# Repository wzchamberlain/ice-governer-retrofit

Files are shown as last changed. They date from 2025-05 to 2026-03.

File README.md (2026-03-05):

# ICE-Governor-Retrofit

## Rationale & Goal

The goal of this project is to provide a low cost electronic governor retrofit for small/carburetor engines to replace poor, worn, malfunctioning, or destroyed governors. Typical off-the-shelf variants cost in excess of $100 USD, surpassing the remaining value of the small engine they might be applied to. The target deployment engine this project is built for specifically is a 4000W single phase (true) generator, where the engine must be kept at a steady 3600 RPM or 3000 RPM for 60 Hz or 50 Hz respectively. Provisions should be made in the design to allow for dynamic target speed setting both for fine tuning or for a dynamic governor, such as in a small tractor or ride on lawnmower, perhaps even a gas powertool.

## Pin Count

### Pin Planning
Max IO: 6 pins. One of the potentiometers should be limited to range of 2.5V to HIGH so that I can be used on the RESET line of the ATTiny (GROUND/LOW Pull is reset active).
1. Spark Detect +
    - Bit 2 (Pin7) is the external interrupt pin and would be preferred, however there is only one external interrupt.
2. Spark Detect -
    - Bit 0 (Pin 5) for convince, has Pin Change Interrupt.
3. Servo PWM
    - Bit 4 or Bit 1 should be used for the non-inverted PWM output.
    - Pin 6 or Pin 3.
4. Speed (Position) Potentiometer
    - Potentiometer for speed
    - (Optional) Grounding/High switch to signal off.
        - Cannot be on reset (Bit 5, Pin 1)
5. Integral Potentiometer
6. Derivative Potentiometer

### Signaled Shutoff Plan
This variant of the schematic and pin planning uses the switch (SPDT) to signal the ATTiny to ramp down (and stall) the engine before entering a sleep state. This will result in a parasitic draw when in sleep/off to allow the microcontroller to wake up and for the LDO Voltage Regulator to down-regulate the battery. This is done as a trade off to make operation safer by ensuring that the throttle body is closed to prevent a runaway. The battery planned is a relatively larger 9V box battery.

#### By Pin Number
1. Second Order Reaction
2. First Order Reaction
3. Speed Set and Sleep Trigger
4. GND
5. Spark Trigger
6. Servo Position PWM
7. Spark Trigger
8. VCC

#### By Port Number (All Port B)
0. Spark Trigger
1. Servo Position PWM
2. Spark Trigger
3. First Order Reaction
4. Speed Set and Sleep Trigger
5. Second Order Reaction

#### Schematic Plan
Schematic

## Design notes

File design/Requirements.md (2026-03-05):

# Requirements Design Document
This document outlines the requirements of this project in order to complete the goal of providing a electronic throttle governance (by speed) retrofit for small engines.
At the writing of this section, previous considerations had been made and hardware selections made. As such this document regards **software requirements** under the constraints of the previously selected hardware rather than the *hardware requirements* that dictated the hardware selections.

## Functional Requirements
These are the functional objectives that the software must achieve.

1. Produce a PWM signal at 50 Hz (t=20 ms) with duty cycle of 1-2 ms (5-10 %) to control throttle positioning servo (sg90).
2. Time spark pulse intervals.
3. Mark spark pulse polarities to eliminate transience.
4. Analog read for speed set point. *Alteratively as Position Error constant.*
5. Interrupt read on speed set to enable sleep-wake behaviour.
6. Analog read for corrective response speed/aggression. *Alternatively as Integral Error constant.*
7. Analog read for corrective response dampening. *Alternatively as Derivative Error constant.*

## Assignments of functions on ATTiny85
The ATTiny85 provides all the needed functional peripherals to achieve these functions, but they must be configured to connect the bus functions and peripheral components as such.

Needed peripheral assignments:

| Function/Peripheral | Count | Reason/Assignment | Port Number(s) | Pin Number(s) |
| ---: | ----: | :--- | ---: | ---: |
| PWM (Timer with prescale and dedicated reset output) | 1x | PWM to pin for throttle servo control signal. Outputs directly to pin. | 1 | 6x |
| Timer (with prescale) | 1x | For measurement of timing of spark pulses (for engine speed calculation and Process). No physical IO, logically controlled by software interrupts. | N/A | N/A |
| PCINT (Process Interrupt) | 2x | For catchment of spark trigger events. Mapped to spark sense pins. | 0, 2 | 5, 7 |
| PCINT/INT | 1x (Assigned on sleep) | For wake from sleep state. Mapped to speed/proportion response pin. | 4 | 3 |
| ADC | 3x | ADC measurement of trim potentiometers for adjustment of Set Point and/or PID constants | 3, 4, 5 | 1, 2, 3 |

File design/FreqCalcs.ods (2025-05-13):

RPM | Hz | T/c (s) | 1/2 RPM | 1/2 Hz | 2 T/c (s) | Delta T/c (s) | Delta 2T/c (s) | Delta T/c (ms) | Delta 2T/c (ms) | Delta T/c (μm) | Delta 2T/c (μm) | Delta T/c (ns) | Delta 2T/c (ns) | c/1MHz | c/4MHz | c/10MHz | c/20MHz | 2c/1MHz | 2c/4MHz | 2c/10MHz | 2c/20MHz
10 | 0.166666666666667 | 6 | 5 | 0.0833333333333333 | 12 | 3 | 6 | 3000 | 6000 | 3000000 | 6000000 | 3000000000 | 6000000000 | 6000000 | 24000000 | 60000000 | 120000000 | 12000000 | 48000000 | 120000000 | 240000000
20 | 0.333333333333333 | 3 | 10 | 0.166666666666667 | 6 | 1 | 2 | 1000 | 2000 | 1000000 | 2000000 | 1000000000 | 2000000000 | 3000000 | 12000000 | 30000000 | 60000000 | 6000000 | 24000000 | 60000000 | 120000000
30 | 0.5 | 2 | 15 | 0.25 | 4 | 0.5 | 1 | 500 | 1000 | 500000 | 1000000 | 500000000 | 1000000000 | 2000000 | 8000000 | 20000000 | 40000000 | 4000000 | 16000000 | 40000000 | 80000000
40 | 0.666666666666667 | 1.5 | 20 | 0.333333333333333 | 3 | 0.3 | 0.6 | 300 | 600 | 300000 | 600000 | 300000000 | 600000000 | 1500000 | 6000000 | 15000000 | 30000000 | 3000000 | 12000000 | 30000000 | 60000000
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

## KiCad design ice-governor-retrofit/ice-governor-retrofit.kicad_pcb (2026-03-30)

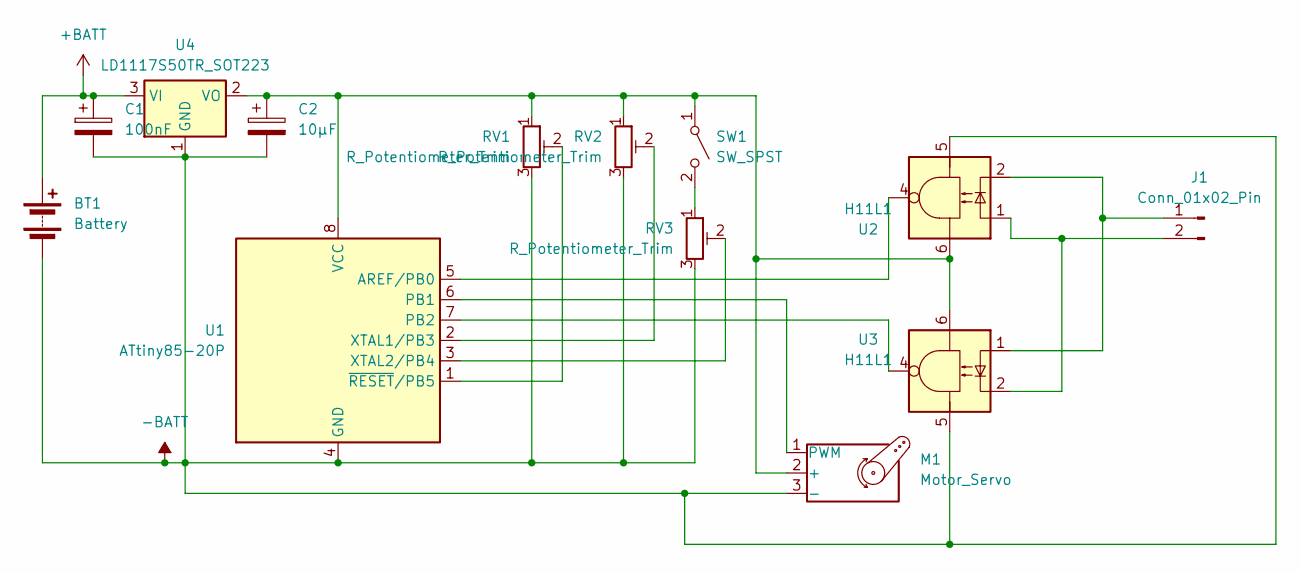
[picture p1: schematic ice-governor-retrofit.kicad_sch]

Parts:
BT1: Battery; BatteryHolder_Eagle_12BH611-GR
C1: 100nF; CP_Radial_D5.0mm_P2.50mm
C2: 10μF; CP_Radial_D5.0mm_P2.50mm
J1: Conn_01x02_Pin; PinHeader_1x02_P2.54mm_Vertical
M1: Motor_Servo; PinHeader_1x03_P2.54mm_Vertical
RV1, RV2, RV3: R_Potentiometer_Trim; Potentiometer_Vishay_43_Horizontal
SW1: SW_SPST; PinHeader_1x02_P2.54mm_Vertical
U1: ATtiny85-20P; DIP-8_W7.62mm
U2, U3: H11L1; DIP-6_W7.62mm
U4: LD1117S50TR_SOT223; SOT-223-3_TabPin2

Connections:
+BATT: BT1.1 (+), C1.1, U4.3 (VI)
-BATT: BT1.2 (-), C1.2, C2.2, M1.3 (-), RV1.3, RV2.3, RV3.3, U1.4 (GND), U2.5, U3.5, U4.1 (GND)
unnamed: J1.1, U2.2, U3.1
unnamed: J1.2, U2.1, U3.2
unnamed: C2.1, M1.2 (+), RV1.1, RV2.1, SW1.1 (A), U1.8 (VCC), U2.6, U3.6, U4.2 (VO)
unnamed: M1.1 (PWM), U1.6 (PB1)
unnamed: RV3.1, SW1.2 (B)
unnamed: U1.5 (AREF/PB0), U2.4
unnamed: U1.7 (PB2), U3.4
unnamed: RV2.2, U1.2 (XTAL1/PB3)
unnamed: RV3.2, U1.3 (XTAL2/PB4)
unnamed: RV1.2, U1.1 (~RESET/PB5)

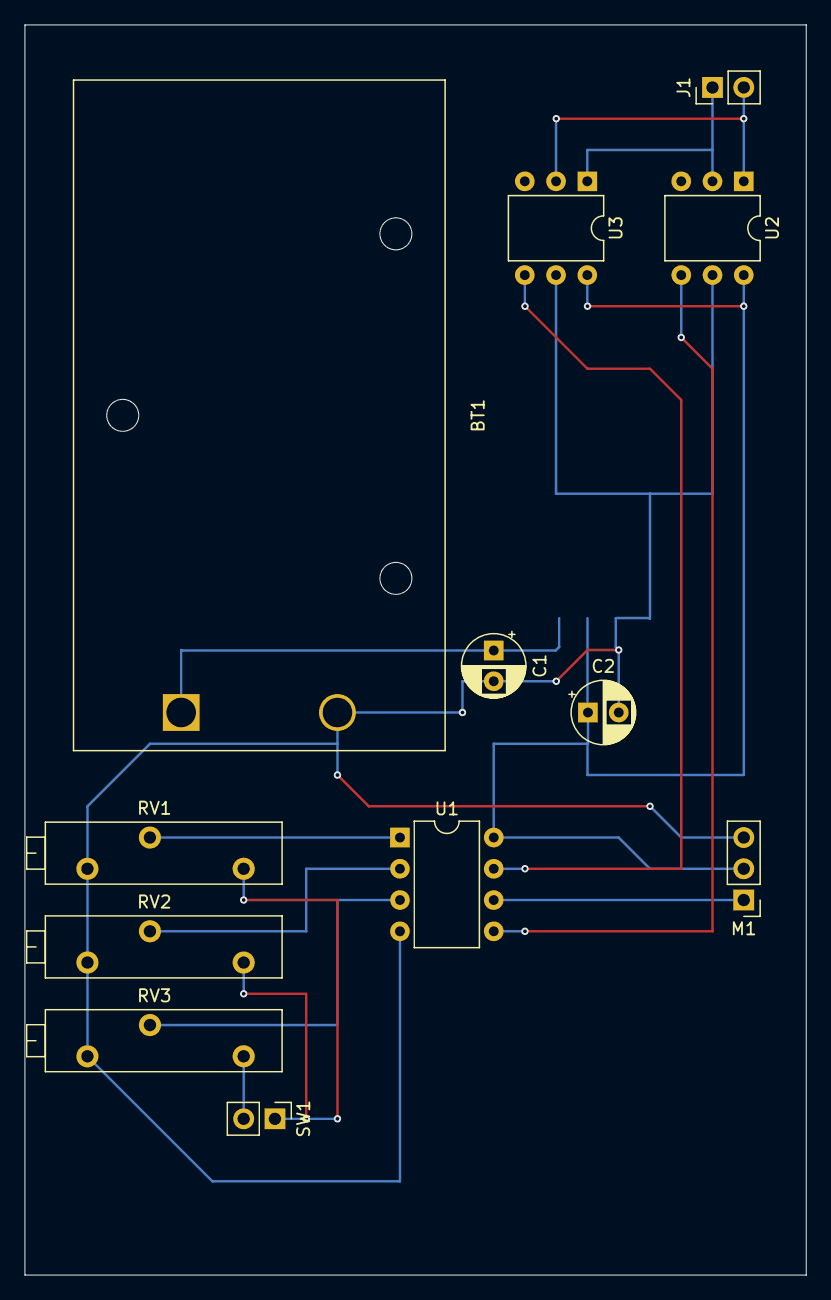
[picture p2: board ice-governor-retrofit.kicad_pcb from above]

Board: 2 copper layers, 63.5 x 101.6 mm, 13 parts (1 on the bottom side), 12 nets.

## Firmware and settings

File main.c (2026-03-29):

#include <avr/io.h>
#include <avr/sleep.h>
#include <avr/interrupt.h>
#include <stdint.h> // actually comes from avr, is override by compiler
#include <stdbool.h> // these booleans are actually 1 byte blocks

#define SERVO_PIN PB1 // servo PWM output pin
#define SPARK_PIN0 PB0 // (+) polar spark detect pin
#define SPARK_PIN1 PB2 // (-) polar spark detect pin
#define POS_POT_PIN PB4 // position constant trim potentiometer pin
#define INT_POT_PIN PB3 // integral constant trim potentiometer pin
#define DER_POT_PIN PB5 // derivative constant trim potentiometer pin
#define AWAKE_PIN POS_POT_PIN // pin for wake from sleep and send to sleep (alias for position constant trim potentiometer pin)

#define MIN_SERVO 7
#define MAX_SERVO 15

#define TARGET_DURATION 4166 // target duration of a spark cycle in ticks
#define DIFFERENCE_MULTIPLIER 1
#define DIFFERENCE_DIVISOR 1
#define DERIVATIVE_MULTIPLIER 1
#define DERIVATIVE_DIVISOR 1
#define INTEGRAL_MULTIPLIER 1
#define INTEGRAL_DIVISOR 1
#define FINAL_BITSHIFT 24

volatile uint8_t timer_rollover = 0; // used for time tracking.
volatile bool timer_double_roll = false;
volatile bool is_sleep_set = false;
volatile uint8_t pos_pot_val = 128; // let pos_pot_val of 128 mark a target of 3600rpm (60Hz)
volatile uint8_t int_pot_val = 128;
volatile uint8_t der_pot_val = 128;
volatile uint16_t last_duration = TARGET_DURATION;
volatile uint16_t last_error = 0;
volatile int32_t last_integral = 0;

void setup_pins() {
    // Set up port and pins
    // Set as output pins
    DDRB |= _BV(SERVO_PIN);

    // Set as input pins
    DDRB &= ~_BV(SPARK_PIN0);
    DDRB &= ~_BV(SPARK_PIN1);
    DDRB &= ~_BV(POS_POT_PIN);
    DDRB &= ~_BV(INT_POT_PIN);
    DDRB &= ~_BV(DER_POT_PIN);
    DDRB &= ~_BV(AWAKE_PIN); // This is duplicate, but placed in case of future modification or chipset change

    // Set pullup resistors (as required by OPTO-schmitt)
    PORTB |= _BV(SPARK_PIN0);
    PORTB |= _BV(SPARK_PIN1);

    // Disable pullup resistors on analog input trim potentiometers
    PORTB &= ~_BV(POS_POT_PIN);
    PORTB &+ ~_BV(INT_POT_PIN);
    PORTB &= ~_BV(DER_POT_PIN);
}

void setup_timer() {
    // set timer interrupt on overflow
    // disable interaction with pins for timer 0
    TCCR0A &= ~_BV(COM0A0);
    TCCR0A &= ~_BV(COM0A1);
    TCCR0A &= ~_BV(COM0B0);
    TCCR0A &= ~_BV(COM0B1);
    // set to "normal" counter mode
    TCCR0A &= ~_BV(WGM00);
    TCCR0A &= ~_BV(WGM01);
    TCCR0B &= ~_BV(WGM02);

    // 8x pre-scaler @ 1 MHz -> 7,500,000 tick/min | 125,000 tick/sec (2083.333333333 tick/60Hz for 2 stroke, 4166.666666667 tick/30Hz for 4 stroke)
    TCCR0B &= ~_BV(CS02);
    TCCR0B |= _BV(CS01);
    TCCR0B &= ~_BV(CS00);

    // disable force output compare registers?
    TCCR0B &= ~_BV(FOC0A);
    TCCR0B &= ~_BV(FOC0B);

    // set interrupt
    TIMSK &= ~_BV(OCIE0A); // no interrupt on OC0A match
    TIMSK &= ~_BV(OCIE0B); // no interrupt on OC0B match
    TIMSK |= _BV(TOIE0); // interrupt on timer 0 overflow
}

void setup_adc() {
    // use prescaler of 8, (1MHz / 8 = 125kHz, >=50kHz, <=200kHz)
    ADCSRA |= _BV(ADPS0);
    ADCSRA |= _BV(ADPS1);
    ADCSRA &= ~_BV(ADPS2);
    // enable ADC
    ADCSRA |= _BV(ADEN);
    // disable conversion completion interrupt (using busy wait, don't want an ISR)
    ADCSRA &= ~_BV(ADIE);
    // do not use auto triggering of ACD, will use a schedule in main loop to run this
    ADCSRA &= ~_BV(ADATE);
    
    // disable bipolar sampling (only reading GND to VCC)
    ADCSRB &= ~_BV(BIN);
    ADCSRB &= ~_BV(IPR);
    
    // set voltage reference to VCC
    ADMUX &= ~_BV(REFS0);
    ADMUX &= ~_BV(REFS1);
    ADMUX &= ~_BV(REFS2);
    // set left shift (only care about 8 MSb, 10bit precision not needed so this makes reading out byte easier)
    ADMUX |= _BV(ADLAR);

    // disable digital inputs for ADC pins NOTE: need to enable this entering sleep?
    DIDR0 |= _BV(ADC0D);
    DIDR0 |= _BV(ADC2D);
    DIDR0 |= _BV(ADC3D);
}

void set_pin_ints_run(){ // set up pin interrupts for running mode
    PCMSK |= _BV(PCINT0);
    PCMSK &= ~_BV(PCINT1);
    PCMSK |= _BV(PCINT2);
    PCMSK &= ~_BV(PCINT3);
    PCMSK &= ~_BV(PCINT4);
    PCMSK &= ~_BV(PCINT5);
}

void set_pin_ints_sleep() { // set up pin interrups for sleep mode (spark + RPM POT)
    PCMSK |= _BV(PCINT0);
    PCMSK &= ~_BV(PCINT1);
    PCMSK |= _BV(PCINT2);
    PCMSK &= ~_BV(PCINT3);
    PCMSK |= _BV(PCINT4);
    PCMSK &= ~_BV(PCINT5);
    DIDR0 &= ~_BV(ADC2D);
}

void init_pwm() {
    // use prescaler x128 to provide maximal resolution within 50Hz @ Main CLK 1MHz [(1Mhz / 128) = 7812.5Hz,  (7812.5Hz / 50Hz) = 156.25 Cycles]
    TCCR1 &= ~_BV(CS10);
    TCCR1 &= ~_BV(CS11);
    TCCR1 &= ~_BV(CS12);
    TCCR1 |= _BV(CS13);

    // set to PWM mode (A output) (similar effect to previous, ORC1C match clears)
    TCCR1 |= _BV(PWM1A);
    TCCR1 &= ~_BV(COM1B0);
    TCCR1 |= _BV(COM1A1);
    // disable PWM mode B output
    GTCCR &= ~_BV(PWM1B);
    GTCCR &= ~_BV(COM1B0);
    GTCCR &= ~_BV(COM1B1);

    // no interrupts for timer 1
    TIMSK &= ~_BV(OCIE1A);
    TIMSK &= ~_BV(OCIE1B);
    TIMSK &= ~_BV(TOIE1);

    // reset timer at 156 cycles (-1 since 0 is compared)
    OCR1C = 155;
    // duty cycle is 5%-10%, setting to min as a default [MIN: (156.25 * 5%) - 1 = 6.8125 ~= 7, MAX: (156.25 * 10%) - 1 = 14.625 ~= 15]
    OCR1A = MIN_SERVO;
}

void set_throttle_by_percent(uint8_t percent) {
    uint8_t new_val = MIN_SERVO;
    new_val += (percent * (MAX_SERVO - MIN_SERVO)) / 100;
    OCR1A = new_val;
}

void set_throttle_by_uint8(uint8_t input) {
    uint8_t new_val = MIN_SERVO;
    new_val += (input * (MAX_SERVO - MIN_SERVO)) / 255;
    OCR1A = new_val;
}

uint8_t get_throttle_as_uint8() {
    return OCR1A;
}

void close_throttle() {
    OCR1A = MIN_SERVO;
}

void wide_open_throttle() {
    OCR1A = MAX_SERVO;
}

// timer 0 (time counter) overflow interrupt
ISR (TIMER0_OVF_vect) {
    timer_rollover++; // just increment the timer
    if (timer_rollover >= 255) { // make note of the double rollover for throttle calculations
        timer_rollover = 0;
        timer_double_roll = true;
    }
}

// PCINT interrupt
ISR (PCINT0_vect) {
    if (is_sleep_set) { // sleep mode, wake
        wide_open_throttle();
        set_pin_ints_run();
        setup_adc();
        setup_timer();
        init_pwm();
        timer_double_roll = false;
        timer_rollover = 0;
        TCNT0 = 0;
        // TODO: reset/restart sub controllers
    } else { // normal running, spark detected
        if (timer_double_roll) {
            // engine is too slow to even track. Just hit the limiter so a reading can even be achieved.
            // if this causes thrashing in impl, then we need to widen the rollover integer
            wide_open_throttle();
            // clear timers
            timer_double_roll = false;
            timer_rollover = 0;
            TCNT0 = 0;
        } else {
            uint16_t rotation_duration = TCNT0; // set low byte to value currently in timer
            rotation_duration += timer_rollover << 8; // set high byte from rollover
            // clear timer so it can continue tracking
            timer_rollover = 0;
            TCNT0 = 0;
            // calculate error
            int32_t error = rotation_duration - TARGET_DURATION;
            // calculate time delta
            int32_t duration_delta = rotation_duration - last_duration;
            // find difference between counted and setpoint
            int32_t time_difference = error * pos_pot_val * DIFFERENCE_MULTIPLIER / (128 * DIFFERENCE_DIVISOR);
            // find derivative
            int32_t time_derivative = (error - last_error) * der_pot_val * DERIVATIVE_MULTIPLIER / (128 * duration_delta * DERIVATIVE_DIVISOR);
            // find integral
            int32_t time_integral = (last_integral + (error * duration_delta)) * int_pot_val * INTEGRAL_MULTIPLIER / (128 * INTEGRAL_DIVISOR);
            int32_t pid_out = time_difference + time_derivative + time_integral;
            uint8_t adjust = (pid_out < 0) ? ((-pid_out) >> FINAL_BITSHIFT) : (pid_out >> FINAL_BITSHIFT);
            uint8_t current_throttle = get_throttle_as_uint8();
            if (pid_out < 0 && adjust >= current_throttle) {
                close_throttle();
            } else if (pid_out < 0) {
                set_throttle_by_uint8(current_throttle - adjust);
            } else if (current_throttle >= current_throttle) {
                wide_open_throttle();
            } else {
                set_throttle_by_uint8(current_throttle + adjust);
            }
        }
    }
}

int main(void) {
    setup_pins(); // set up port B pins
    setup_timer(); // set up timer 0 for rpm measure
    setup_adc(); // set up adc block for measurement of pots
    init_pwm(); // set up timer 1 for PWM servo output

    // the forever run loop
    while(true) {
        // measure position pot (PB4, ADC2)
        ADMUX &= ~_BV(MUX0);
        ADMUX |= _BV(MUX1);
        ADMUX &= ~_BV(MUX2);
        ADMUX &= ~_BV(MUX3);
        ADCSRA |= _BV(ADSC); // start the conversion
        loop_until_bit_is_set(ADCSRA, ADIF); // wait for the conversion to finish
        pos_pot_val = ADCH;
        ADCSRA |= _BV(ADIF); // clear the flag
        // measure integral pot (PB3, ACD3)
        ADMUX |= _BV(MUX0);
        ADMUX |= _BV(MUX1);
        ADMUX &= ~_BV(MUX2);
        ADMUX &= ~_BV(MUX3);
        ADCSRA |= _BV(ADSC); // start the conversion
        loop_until_bit_is_set(ADCSRA, ADIF);
        int_pot_val = ADCH;
        ADCSRA |= _BV(ADSC);
        // measure derivative pot (PB5, ADC0)
        ADMUX &= _BV(MUX0);
        ADMUX &= _BV(MUX1);
        ADMUX &= _BV(MUX2);
        ADMUX &= _BV(MUX3);
        ADCSRA |= _BV(ADSC);
        loop_until_bit_is_set(ADCSRA, ADIF);
        der_pot_val = ADCH;
        ADCSRA |= _BV(ADSC);

        // check if sleep/shutdown commanded
        if (pos_pot_val < 2) {
            close_throttle(); // kill engine
            set_pin_ints_sleep();
            is_sleep_set = true;
            // set for powerdown sleep
            MCUCR |= _BV(SM1);
            MCUCR &= ~_BV(SM0);
            // disable brown out detection on sleep. No point in this app
            MCUCR |= _BV(BODS);
            // power reduction measures (shouldn't apply when using powerdown type sleep)
            PRR |= _BV(PRTIM1);
            PRR |= _BV(PRTIM0);
            PRR |= _BV(PRUSI);
            PRR |= _BV(PRADC);
            // enter sleep!
            MCUCR |= _BV(SE);
        }
    }
}

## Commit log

2025-05-13 Initial Commit for Ice-Governer-Retrofit,
    Old repo had an exposed email somewhere in it that I couldn't get rid of
    despite rebasing, so this is effectively a squash of the last two (and
    only previous) commits.
    [FreqCalcs.ods]
2025-12-28 Planning,
    - Modified .gitignore to ignore reference documentation and to ignore drawio backup files.
    - Added ice-governor-retrofit-Signaled-Shutoff.drawio.svg as markdown embeddable schematic.
    - Added ice-governor-retrofit.drawio as schematic and diagram document.
    - Modified README.md to plan pin-outs and to embed schematic.
2025-12-28 Corrected LDO Voltage Regulator Filtering Capacitors,
    - Modified ice-governor-retrofit-Signaled-Shutoff.drawio.svg to reflect updated schematic.
    - Modified ice-governor-retrofit.drawio to add additional filtering capacitor and insert capacitor values.
2025-12-29 Reorganized Files and Directories,
    - Modified .gitignore to reflect updated directory organization.
    - Modified README.md to reference updated image path.
    - Moved FreqCalcs.ods to move the design directory,
    - Moved ice-governor-retrofit.drawio to the design directory.
    - Moved ice-governor-retrofit-Signaled-Shutoff.drawio.svg to the design/assets directory.
    [FreqCalcs.ods]
2026-03-29 Untested MVP of Permanent Setpoint Full PID,
    - Modified main.c to implement PID calculations and dynamic throttle setting.
2026-03-30 Added Perf-Board Layout,
    - Added ice-governor-retrofit KiCad project for schematic and board
    layout(s). Some components subsituted with equivalent footprints.
    [ice-governor-retrofit.kicad_pcb, ice-governor-retrofit.kicad_sch]
